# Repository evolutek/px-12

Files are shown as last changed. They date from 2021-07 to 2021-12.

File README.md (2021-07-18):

# PX-12
The goal of this project is to control 5V pump and EV (such as https://fr.aliexpress.com/item/32792085658.html) via Dynamixel AX-12 protocol (Serial Half-duplex one wire), in order to reduce the number of cable inside the robot for Eurobot by daisy chaining the pump.
## Electronics
The PCB is solder directly at the end of the pump. A connector is present in order to connect the EV on the PCB. 

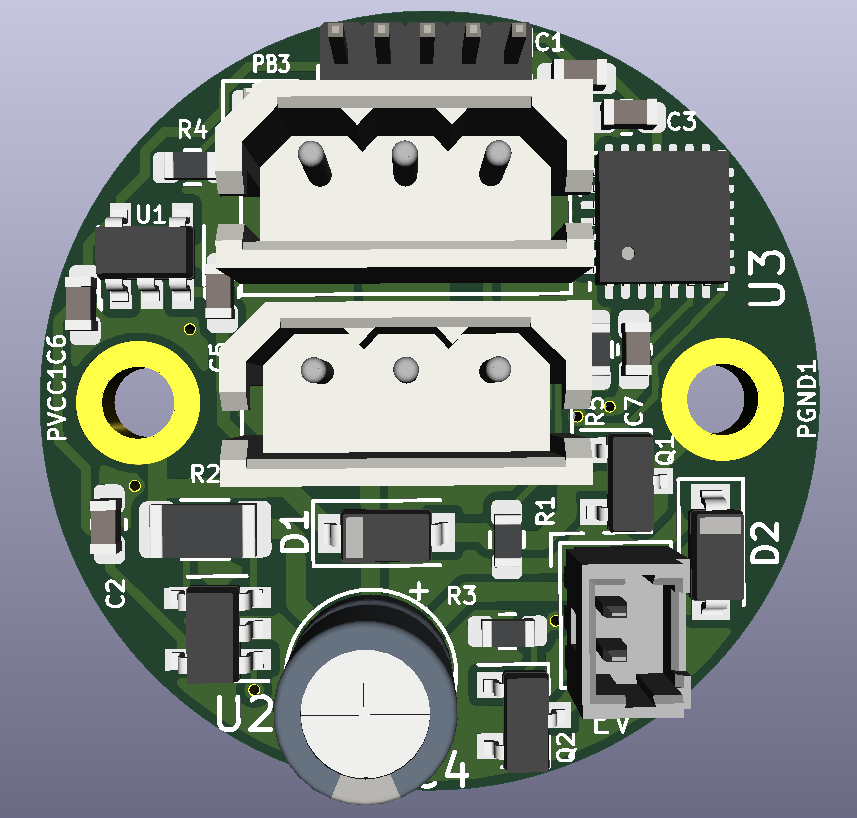
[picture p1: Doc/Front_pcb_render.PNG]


MCU: STM32F042G4\
Current shunt monitor: INA139
R_SHUNT: 0.01 Ohm

## Develloping on the PCB
In order to dev on the MCU you can use either STM32CubeIDE (Eclipse based) or VSCode.
### With VSCode
To dev STM32 chip with VSCode you need to install **stm-helper** from the extension manager in VSCode. After that you can either clone this repo and click on UpdateWorkspace, make sure 
to have the makefile and the .ioc in the source file tree otherwise the extension will not appear at the bottom of the app. Then you can click on **Build** to compile the project and **Download** to flash the MCU.
### Flashing the PCB 
Flashing is done via SWD port in the top of the PCB, in order to flash those PCB you'll need a STLINK V2. 

## TODO
* Add version V1.1 with vaccum sensor to replace the current shunt sensor. 
* Create software for the PX-12.
* Add documentation 
* Add exemple to work with arduino and STM32 platform

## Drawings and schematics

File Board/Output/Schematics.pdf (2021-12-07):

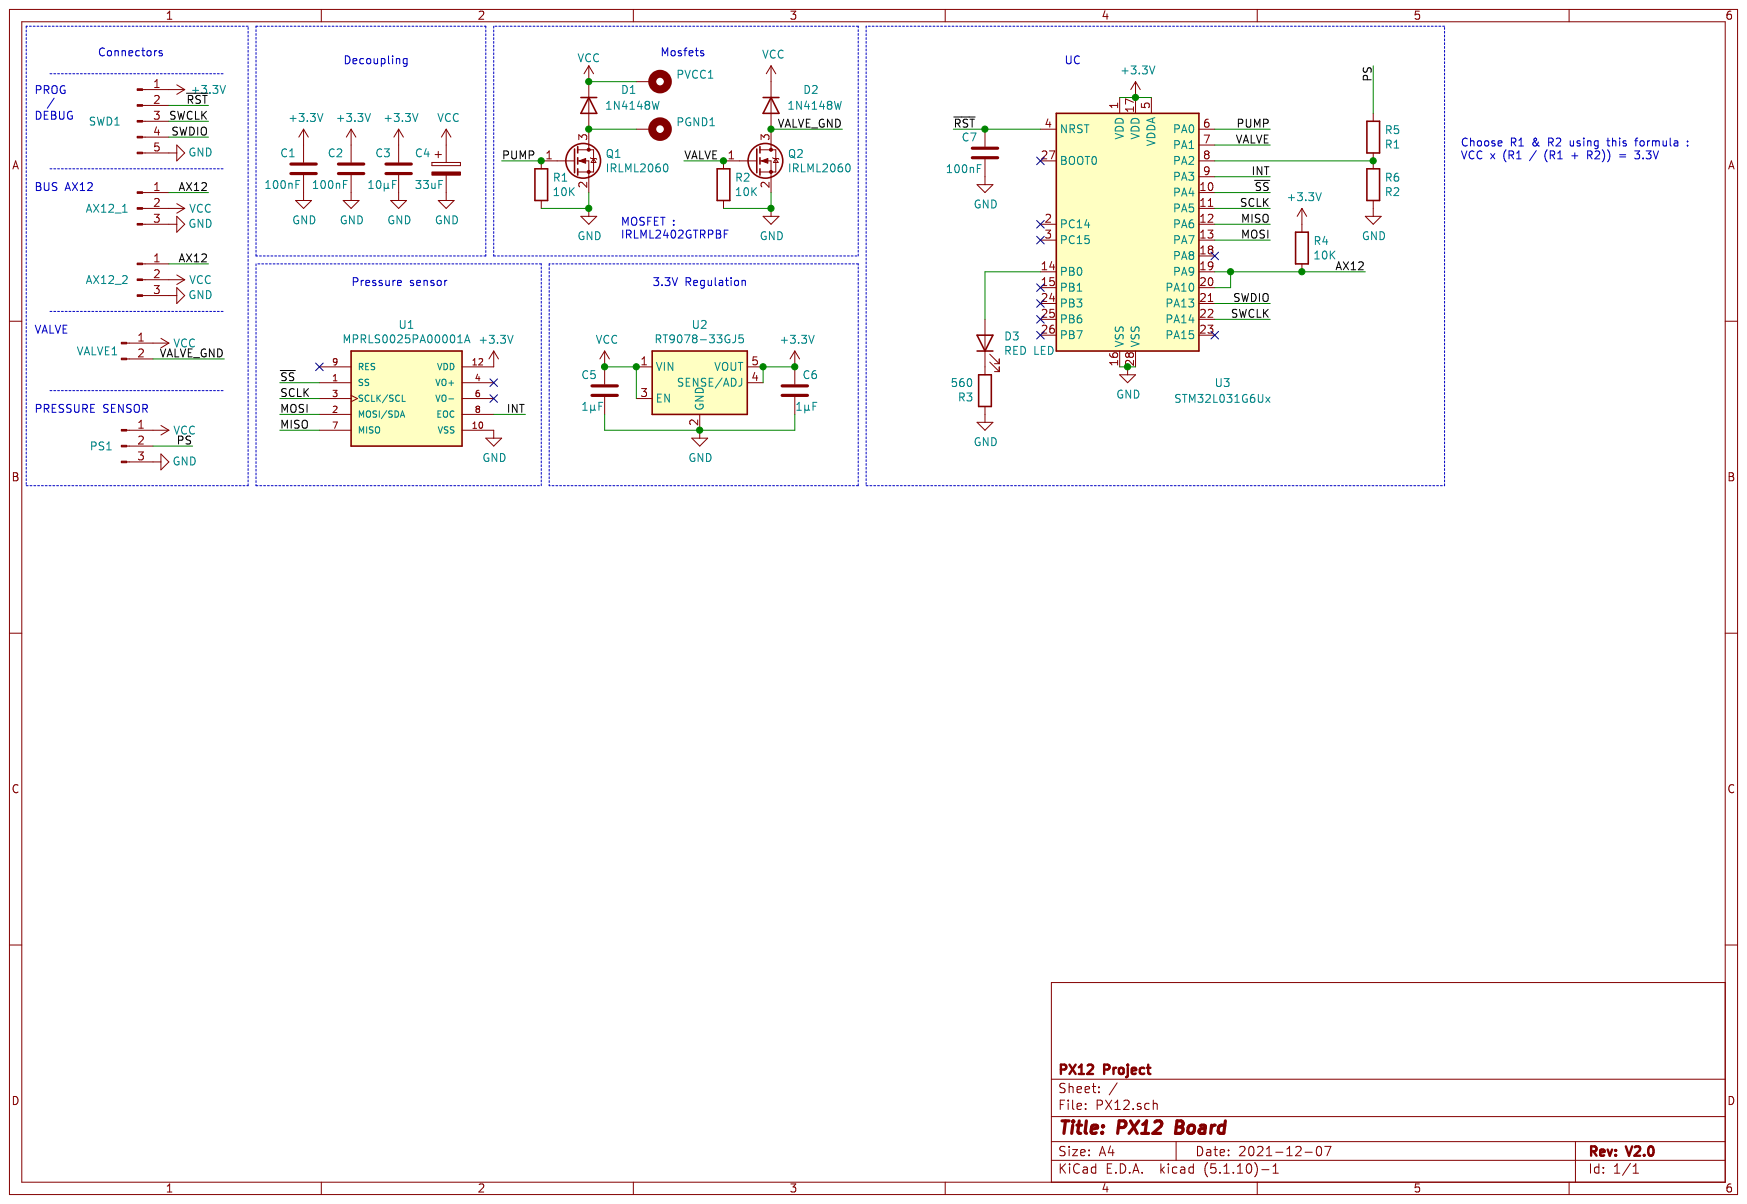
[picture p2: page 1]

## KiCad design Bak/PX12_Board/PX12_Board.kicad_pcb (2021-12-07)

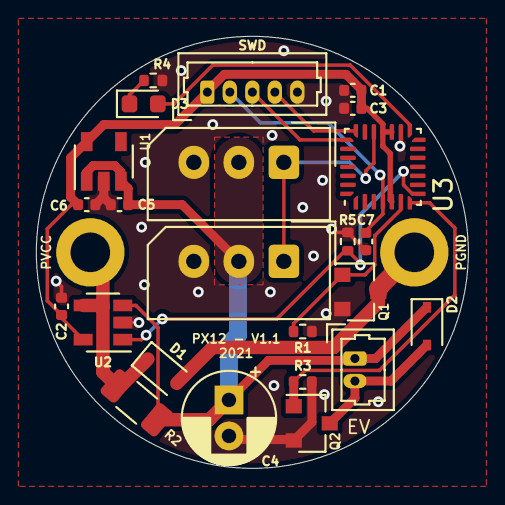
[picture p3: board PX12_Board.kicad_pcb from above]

Board: 2 copper layers, 24.0 x 24.0 mm, 26 parts (0 on the bottom side), 15 nets.

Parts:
AX12_1, AX12_2: Conn_01x03_Male; Molex_SPOX_5267-03A_1x03_P2.50mm_Vertical
C1, C2, C7: 100nF; C_0402_1005Metric
C3: 10µF; C_0402_1005Metric
C4: 33µF; CP_Radial_D5.0mm_P2.00mm
C5, C6: 1µF; C_0402_1005Metric
D1, D2: BAV16WS-7-F; D_SOD-323
D3: LED; LED_0603_1608Metric
PGND: MountingHole_Pad; MountingHole_2.2mm_M2_DIN965_Pad
PVCC: MountingHole_Pad; MountingHole_2.2mm_M2_DIN965_Pad
Q1, Q2: IRLML2060; SOT-23
R1, R3: 10K; R_0402_1005Metric
R2: 0.01; R_1206_3216Metric
R4: 560; R_0402_1005Metric
R5: 3K; R_0402_1005Metric
SWD: Conn_01x05_Male; Molex_PicoBlade_53047-0510_1x05_P1.25mm_Vertical
U1: NCP718xSN330; SOT-23-5
U2: INA139; SOT-23-5
U3: STM32F042G4Ux; QFN-28_4x4mm_P0.5mm
VALVE1: Conn_01x02_Male; Molex_PicoBlade_53047-0210_1x02_P1.25mm_Vertical

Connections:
+3V3: C1.1, C2.1, C3.1, C6.1, SWD.1, U1.5, U2.5, U3.5, U3.17, U3.18
/P-: D1.1, PVCC.1, R2.2, U2.4
/PUMP_GND: D1.2, PGND.1, Q1.3
/VALVE_GND: D2.2, Q2.3, VALVE1.2
GND: AX12_1.3, AX12_2.3, C1.2, C2.2, C3.2, C4.2, C5.2, C6.2, C7.2, Q1.2, Q2.2, R1.2, R3.2, R4.2, R5.2, SWD.5, U1.2, U2.2, U3.16
unnamed: D3.1, R4.1
unnamed: D3.2, U3.15
Pump: Q1.1, R1.1, U3.6
RST: C7.1, SWD.2, U3.4
SERIAL: AX12_1.1, AX12_2.1, U3.19
SWCLK: SWD.3, U3.22
SWDIO: SWD.4, U3.21
VCC: AX12_1.2, AX12_2.2, C4.1, C5.1, D2.1, R2.1, U1.1, U1.3, U2.3, VALVE1.1
Va: R5.1, U2.1, U3.8
Valve: Q2.1, R3.1, U3.7

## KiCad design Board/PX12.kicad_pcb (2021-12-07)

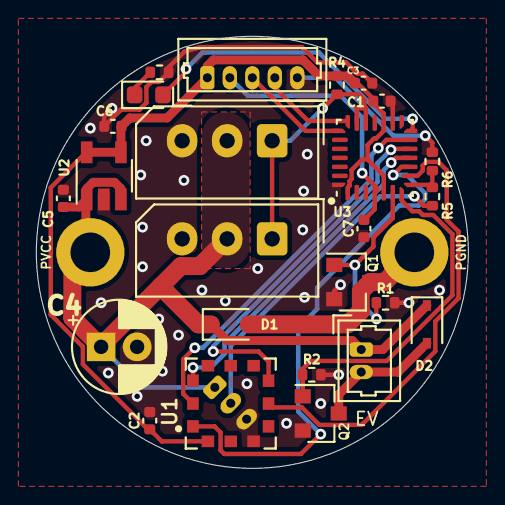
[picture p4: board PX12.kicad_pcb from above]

Board: 2 copper layers, 24.0 x 24.0 mm, 28 parts (0 on the bottom side), 20 nets.

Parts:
AX12_1, AX12_2: Conn_01x03_Male; Molex_SPOX_5267-03A_1x03_P2.50mm_Vertical
C1, C2, C7: 100nF; C_0402_1005Metric
C3: 10µF; C_0402_1005Metric
C4: 33uF; CP_Radial_D5.0mm_P2.00mm
C5, C6: 1µF; C_0402_1005Metric
D1, D2: 1N4148W; D_SOD-323
D3: RED LED; LED_0603_1608Metric
PGND: MountingHole_Pad; MountingHole_2.2mm_M2_DIN965_Pad
PS1: Conn_01x03_Male; Molex_PicoBlade_53047-0310_1x03_P1.25mm_Vertical
PVCC: MountingHole_Pad; MountingHole_2.2mm_M2_DIN965_Pad
Q1, Q2: IRLML2060; SOT-23
R1, R2, R4: 10K; R_0402_1005Metric
R3: 560; R_0402_1005Metric
R5: R1; R_0402_1005Metric
R6: R2; R_0402_1005Metric
SWD1: Conn_01x05_Male; Molex_PicoBlade_53047-0510_1x05_P1.25mm_Vertical
U1: MPRLS0025PA00001A; XDCR_MPRLS0025PA00001A
U2: RT9078-33GJ5; TSOT-23-5
U3: STM32L031G6Ux; QFN-28_4x4mm_P0.5mm
VALVE1: Conn_01x02_Male; Molex_PicoBlade_53047-0210_1x02_P1.25mm_Vertical

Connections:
+3V3: C1.1, C2.1, C3.1, C6.1, R4.1, SWD1.1, U1.12, U2.4, U2.5, U3.1, U3.5, U3.17
/AX12: AX12_1.1, AX12_2.1, R4.2, U3.19, U3.20
/INT: U1.8, U3.9
/MISO: U1.7, U3.12
/MOSI: U1.2, U3.13
/PS: PS1.2, R5.1
/PUMP: Q1.1, R1.1, U3.6
/SCLK: U1.3, U3.11
/SWCLK: SWD1.3, U3.22
/SWDIO: SWD1.4, U3.21
/VALVE: Q2.1, R2.1, U3.7
/VALVE_GND: D2.2, Q2.3, VALVE1.2
/~RST: C7.1, SWD1.2, U3.4
/~SS: U1.1, U3.10
GND: AX12_1.3, AX12_2.3, C1.2, C2.2, C3.2, C4.2, C5.2, C6.2, C7.2, PS1.3, Q1.2, Q2.2, R1.2, R2.2, R3.1, R6.2, SWD1.5, U1.10, U2.2, U3.16, U3.28
unnamed: D1.2, PGND.1, Q1.3
unnamed: D3.1, R3.2
unnamed: D3.2, U3.14
unnamed: R5.2, R6.1, U3.8
VCC: AX12_1.2, AX12_2.2, C4.1, C5.1, D1.1, D2.1, PS1.1, PVCC.1, U2.1, U2.3, VALVE1.1

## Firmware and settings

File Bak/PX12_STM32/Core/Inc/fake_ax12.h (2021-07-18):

#ifndef FAKE_AX12_H
#define FAKE_AX12_H

#include <stdint.h>

#define DEFAULT_SERVO_ID 10
#define DEFAULT_BAUDRATE 1
#define DEFAULT_TORQUE 1

void read_eeprom_from_flash(void);
void write_eeprom_to_flash(void);

void reset(void);
void add_byte(uint8_t byte);

#endif  /* FAKE_AX12_H */

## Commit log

2020-11-22 Add Schematic and pcb file for the pump PCB
    [KLinPump_PCB.kicad_pcb, KLinPump_PCB.sch]
2020-11-22 PCB routed, silkscreen done, need to review
    [KLinPump_PCB.kicad_pcb, KLinPump_PCB.sch]
2020-11-23 Connect pins on the MCU that were not connected
    [KLinPump_PCB.kicad_pcb]
2020-11-23 Interface doc create + pro
    [KLinInterface_PCB.kicad_pcb, KLinInterface_PCB.sch, KLinPump_PCB.sch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]
2020-11-23 Add 3D files
    [22035035.stp, 530470210.stp]
2020-11-23 Fix KLinPump PCB
    [KLinPump_PCB.kicad_pcb, KLinPump_PCB.sch, STM32_base.sch]
2020-11-26 add panel
    [KLinInterface_PCB.sch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]
2020-11-29 New version of the PCB
    [KLinPump_PCB.kicad_pcb, KLinPump_PCB.sch]
2020-11-29 Replace previous name by current
    [PX12_Board-B_Mask.gbr, PX12_Board-B_Paste.gbr, PX12_Board-B_SilkS.gbr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]
2020-11-29 added OSHW logo on the back
    [PX12_Board.kicad_pcb]
2020-11-30 modify the connector pin
    [PX12_Board-B_Mask.gbr, PX12_Board-B_Paste.gbr, PX12_Board-B_SilkS.gbr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]
2020-12-07 Clean repos
    [KLinInterface_PCB.kicad_pcb, KLinInterface_PCB.sch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]
2021-07-16 add stm32 doc
2021-07-16 Add interactive bom
2021-07-16 Add STM32 project
2021-07-18 vscode version + MCU at 48MHz and ADC files
2021-07-18 move 3D folder into kicad folder + 3d render of the pcb in doc
    [22035035.stp, 530470210.stp]
2021-12-07 New version of PCB V1.1
    [PX12_Board-B_CrtYd.gbr, PX12_Board-B_Mask.gbs, PX12_Board-B_SilkS.gbo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]
2021-12-07 Update PCB
    [PX12_Board-B_CrtYd.gbr, PX12_Board-B_Mask.gbs, PX12_Board-B_Paste.gbp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]
2021-12-07 Backup V1.0
    [PX12_Board-B_CrtYd.gbr, PX12_Board-B_Mask.gbs, PX12_Board-B_Paste.gbp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]
2021-12-07 Add V2.0 board
    [22035035.stp, 530470210.stp, PX12.kicad_pcb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]
